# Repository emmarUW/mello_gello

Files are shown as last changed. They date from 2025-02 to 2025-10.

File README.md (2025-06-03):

# mello_gello
Improved models and methods for the Gello robot teleop system



# MELLO GELLO vs. GELLO

Inspired by and based on the original [GELLO project](https://wuphilipp.github.io/gello_site/).

## Key Improvements

- **Motors:** Uses [ROLLER485](https://shop.m5stack.com/products/rollercan-unit-with-bldc-motor-stm32) for better interface durability, I2C pass-through at similar price point
- **Linkages:** Swaps many fully 3D-printed parts with **Gobuilda 1121 aluminum rail** ([details](https://www.gobilda.com/1121-series-low-side-u-channel)).
- **Controller:** Upgraded from U2D2 to [M5 Stack Core3](https://docs.m5stack.com/en/core/CoreS3) with touchscreen, wireless OTA programming, and expanded connectivity.
- **Wireless:** Core3 onboard battery enables **15-20 min untethered runtime**, WiFi control, and flexible power options.
- **Tool Control:** Supports **any I2C input device**, expanding tool control capabilities.
- **Multi-Function Button:** Uses M5 **Key** to zero rotation or pause movement.

---

## Versions:

### UR5e:
The UR5 version of MG is *AVAILABLE* in the Universal Robots/UR5e folder - https://github.com/emmarUW/mello_gello/blob/main/Universal%20Robots/UR5e/README.md

### Franka:
The Franka version of MG is *IN WORK* - in the Franka folder

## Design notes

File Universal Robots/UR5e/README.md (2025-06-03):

UR5 BOM:

This UR5e is a 50%-scale teleop leader for the current model UR5e. All rotation centers should be spatially correct without any software compensation.



Fusion 360 Files - https://a360.co/4katDeD

Purchase:
- Gobuilda:
  - 1121-0008-216 X 1 - https://www.gobilda.com/1121-series-low-side-u-channel-8-hole-216mm-length/
  - 1121-0008-264 x 1 - https://www.gobilda.com/1121-series-low-side-u-channel-10-hole-264mm-length/

 - M5Stack via Digikey:
   - CoreS3 Controller x 1 - https://shop.m5stack.com/products/m5stack-cores3-esp32s3-lotdevelopment-kit
   - Roller485 x 6 - https://shop.m5stack.com/products/roller485-unit-with-bldc-motor-stm32
   - M5 Key x 1 - https://shop.m5stack.com/products/mechanical-key-button-unit
   - M5 Joystick2 x 1 - https://shop.m5stack.com/products/i2c-joystick-2-unit-stm32g030
  


Print:
  - Common Parts:
    - Base
    - Base Adapter
    - Handle Adapter
    - Handle

  - Links 1-5

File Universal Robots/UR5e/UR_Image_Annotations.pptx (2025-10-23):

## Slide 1

264mm/10 hole
Gobuilda
1121-0010-0264

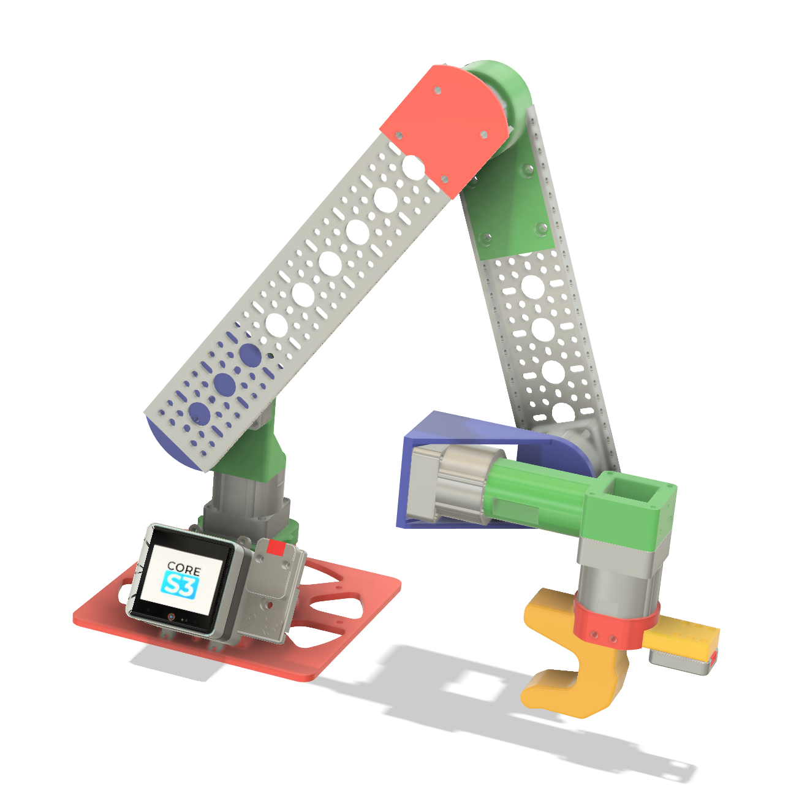
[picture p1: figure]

216mm/8 hole
Gobuilda
1121-0008-0216

DIN RAIL

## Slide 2

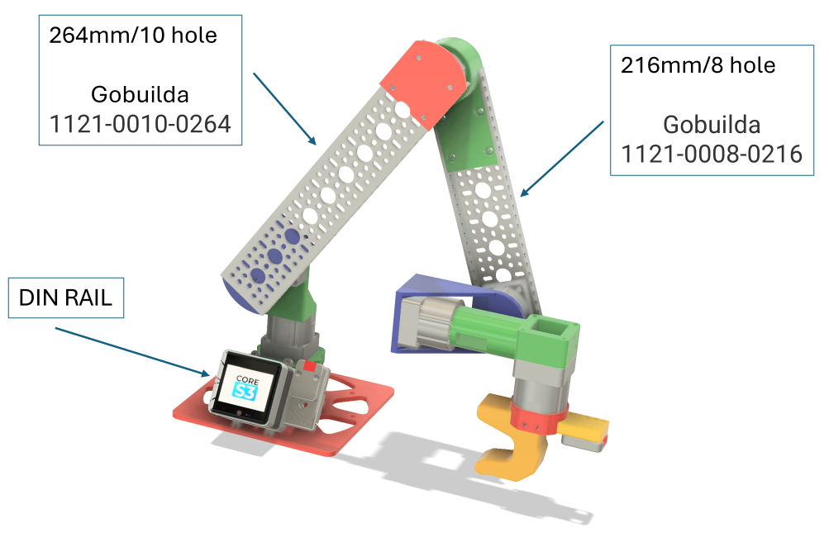
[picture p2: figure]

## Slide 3

264mm/10 hole
Gobuilda
1121-0010-0264

Link_3.stl

216mm/8 hole
Gobuilda
1121-0008-0216

Link_3.stl

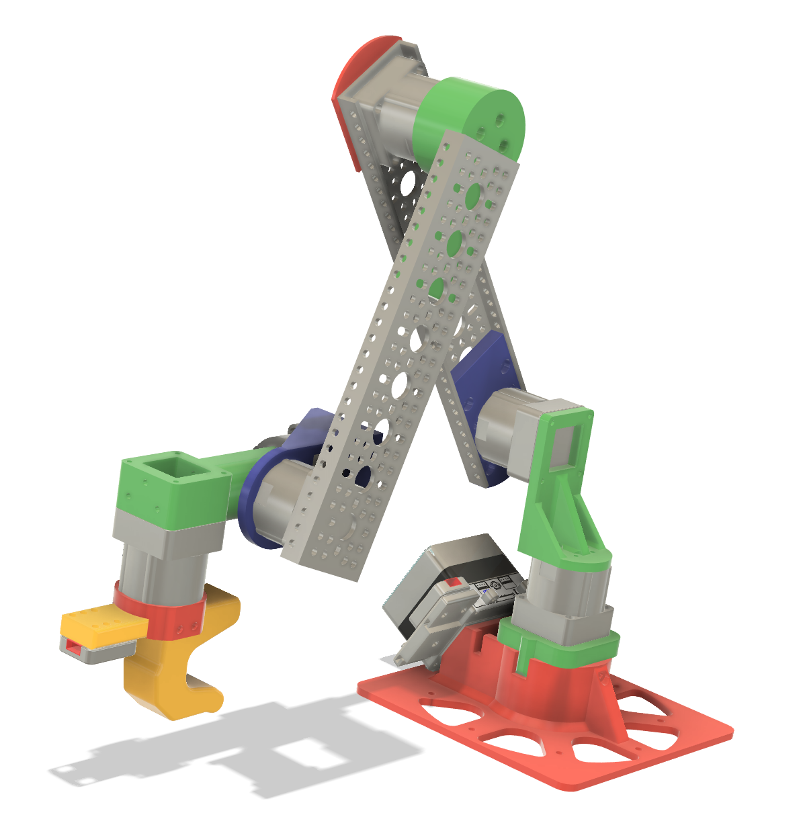
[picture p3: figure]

Common Parts/M5_compatible_handle/*

Link_4.stl

Link_2.stl

Link_7.stl

Link_1.stl

/Common Parts/Base/*

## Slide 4

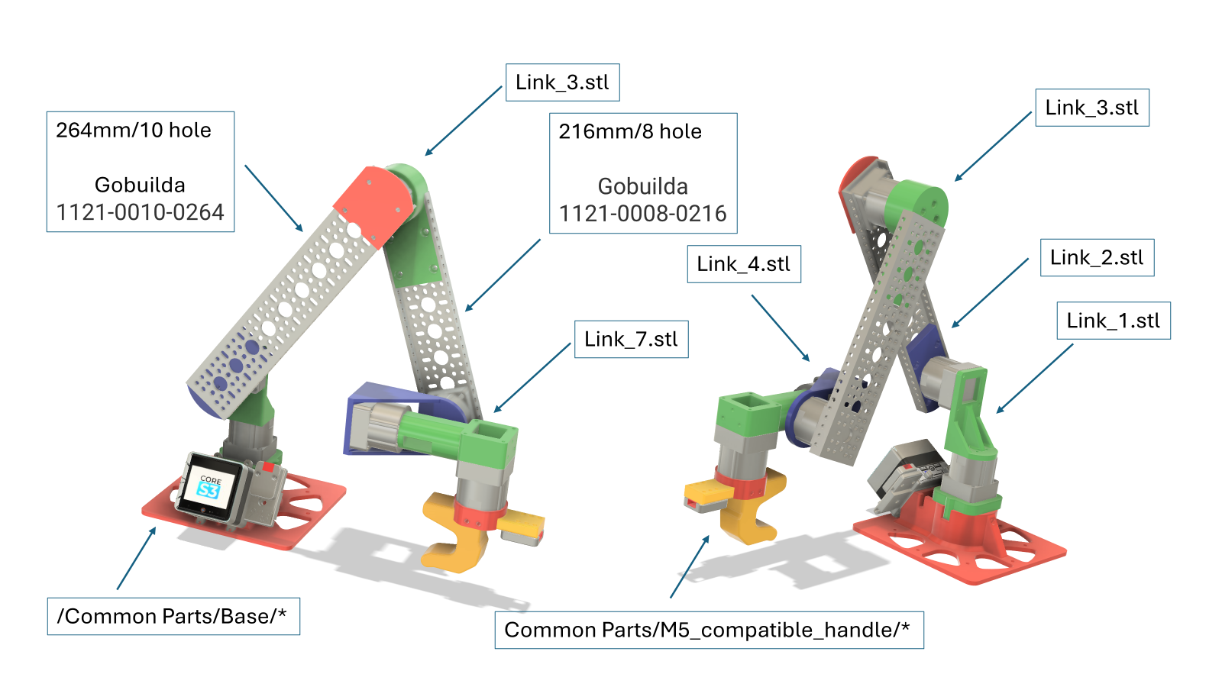
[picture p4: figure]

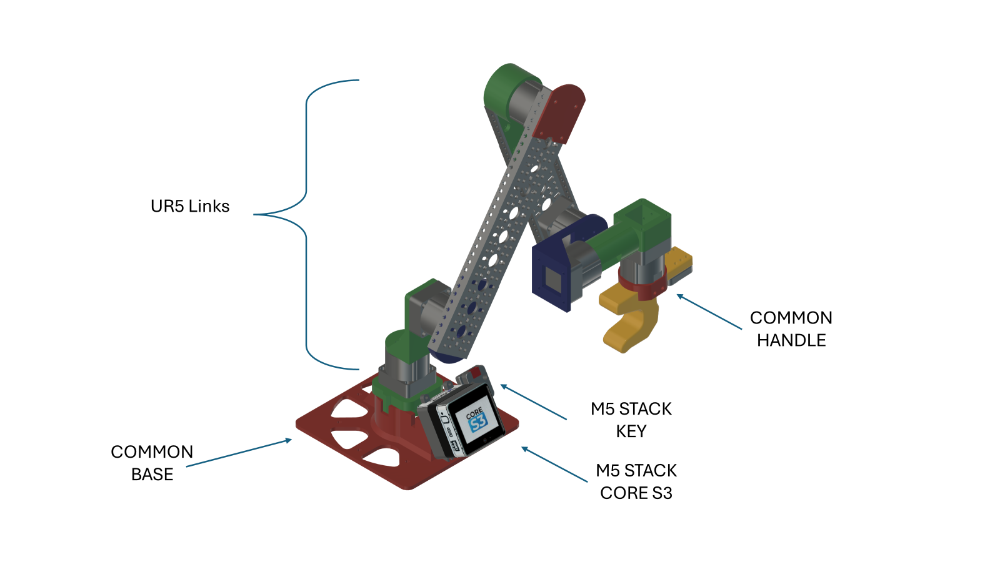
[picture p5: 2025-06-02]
Readme_Schematic.png

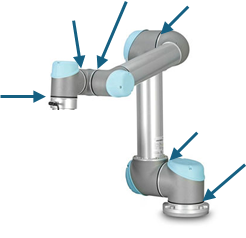
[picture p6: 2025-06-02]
Universal Robots/UR5e/UR.png

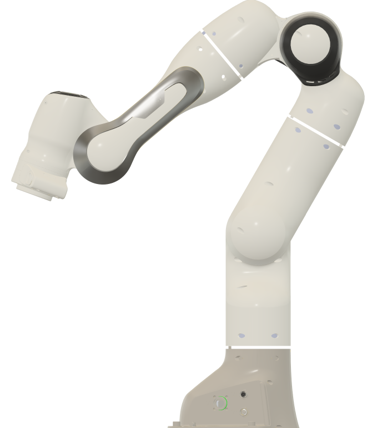
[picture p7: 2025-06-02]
Franka/CAD_franka.png

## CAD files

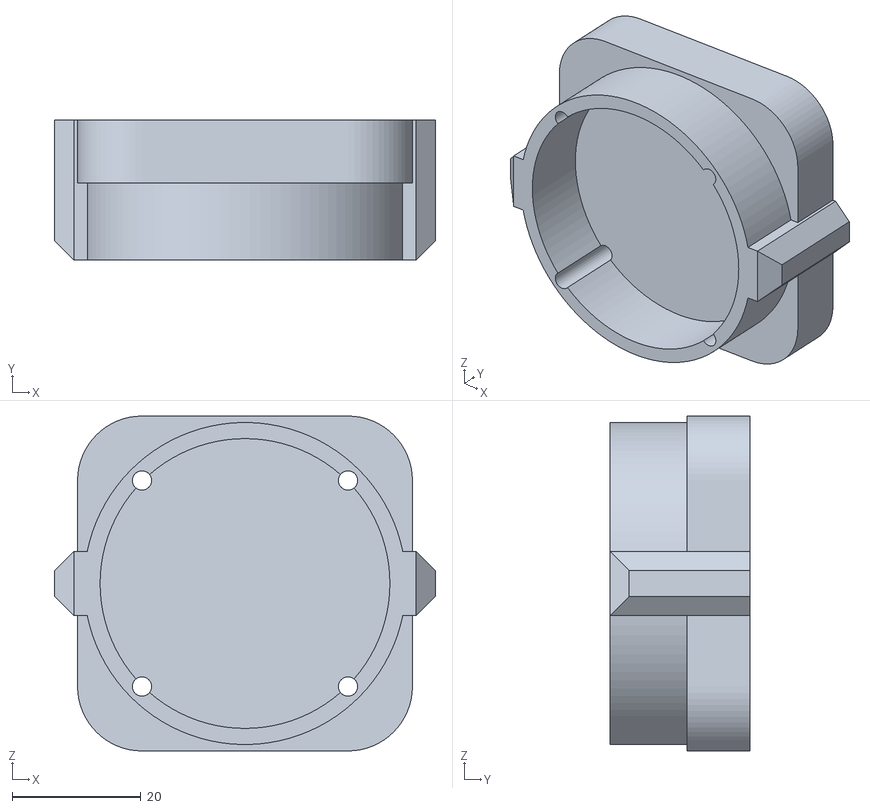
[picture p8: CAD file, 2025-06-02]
Common Parts/Base/base_adapter.stl
59.2 x 21.8 x 52.0

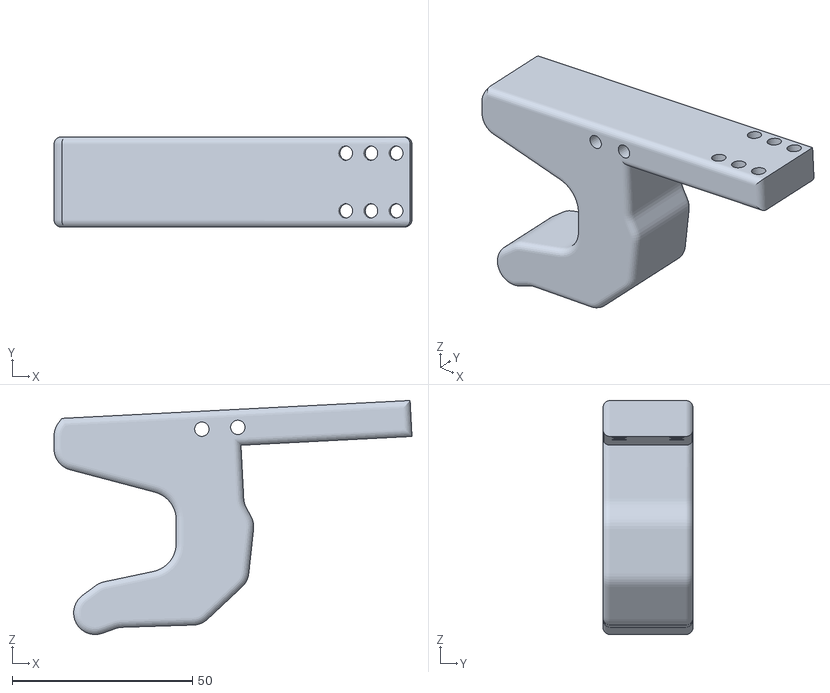
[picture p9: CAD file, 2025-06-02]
Common Parts/M5_compatible_handle/handle_body.stl
99.3 x 25.0 x 64.9

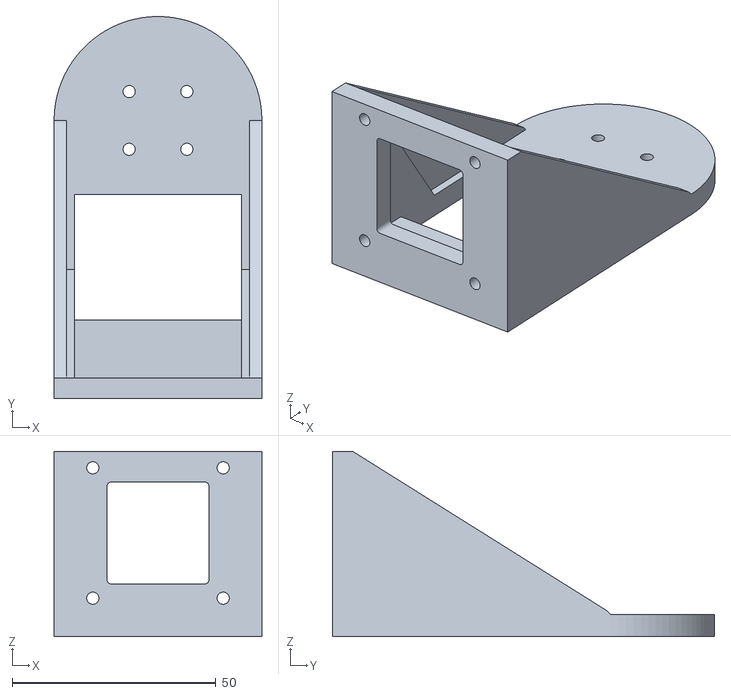
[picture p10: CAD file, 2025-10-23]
Universal Robots/UR5e/Link_4.stl
51.0 x 93.7 x 45.4

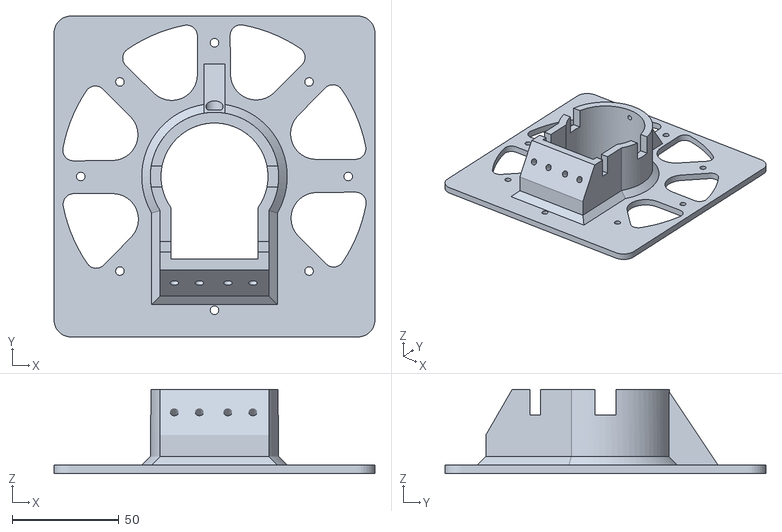
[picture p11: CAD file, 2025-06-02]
Common Parts/Base/Clamp_down_base.stl
150.0 x 150.0 x 39.3

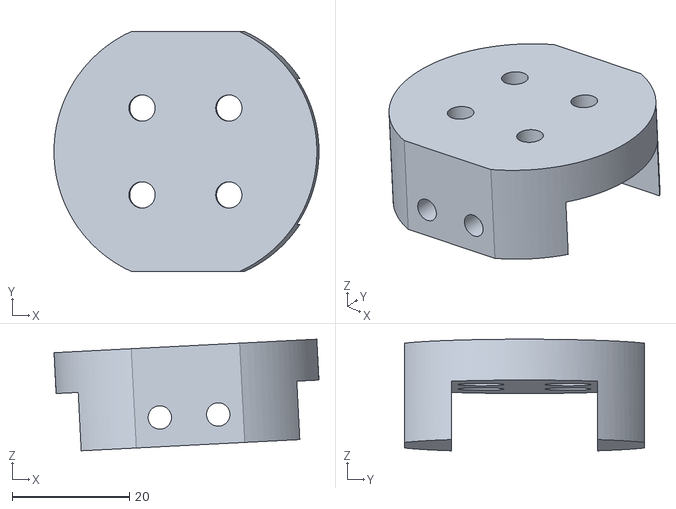
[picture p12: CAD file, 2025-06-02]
Common Parts/M5_compatible_handle/handle_to_motor_adapter.stl
45.3 x 41.0 x 19.1

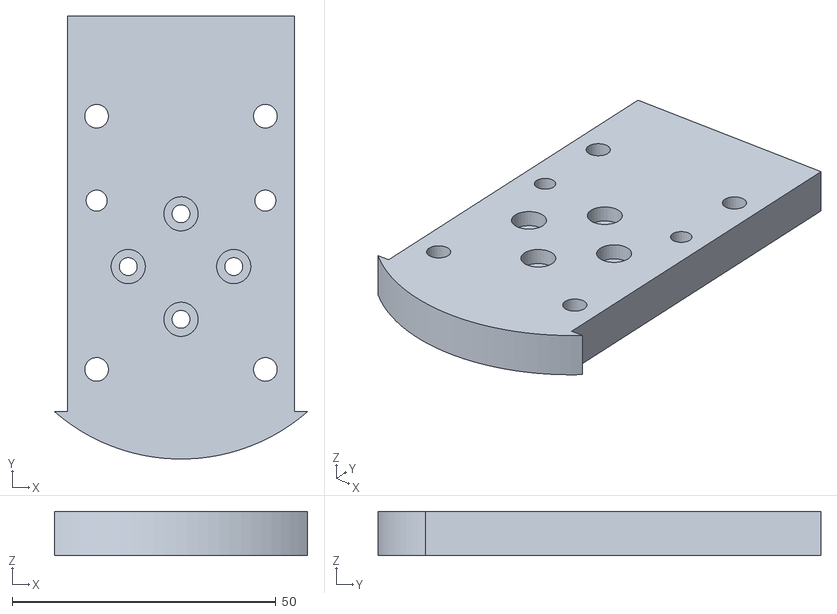
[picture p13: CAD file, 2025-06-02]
Universal Robots/UR5e/Link_2.stl
48.0 x 84.0 x 8.40

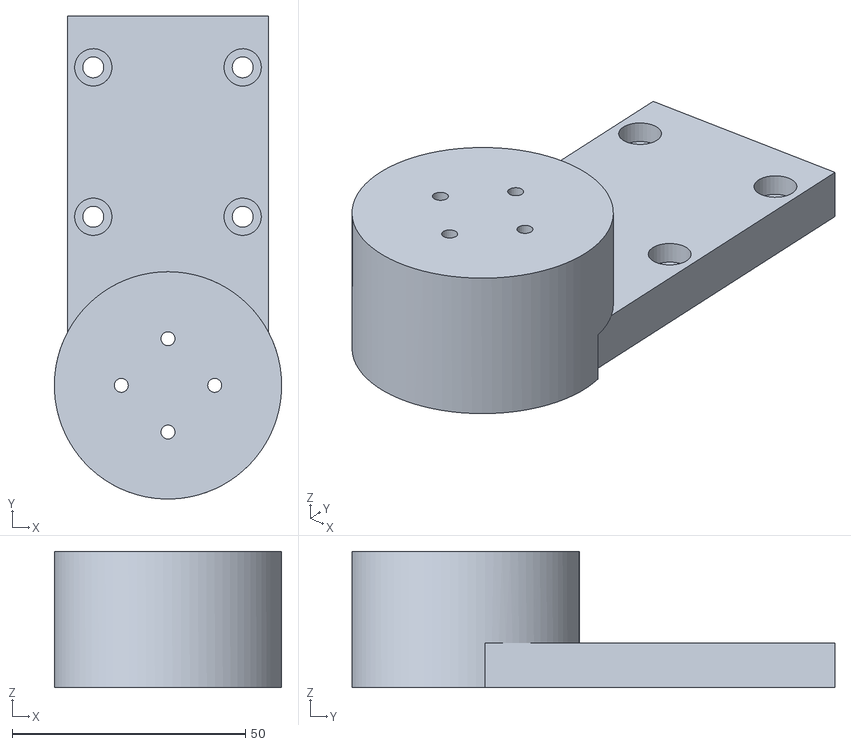
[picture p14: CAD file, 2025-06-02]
Universal Robots/UR5e/Link_3.stl
48.7 x 103.5 x 29.1

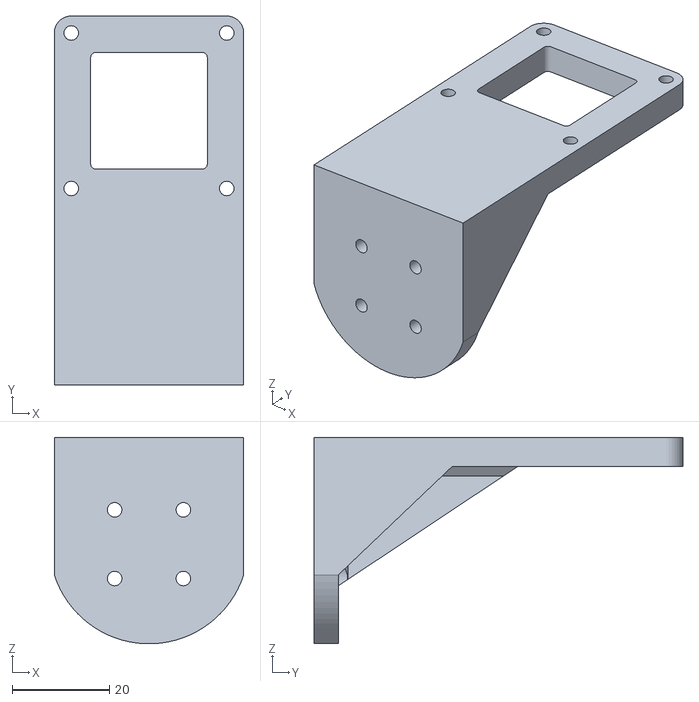
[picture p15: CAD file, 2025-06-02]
Universal Robots/UR5e/Link_1.stl
39.0 x 76.0 x 42.5

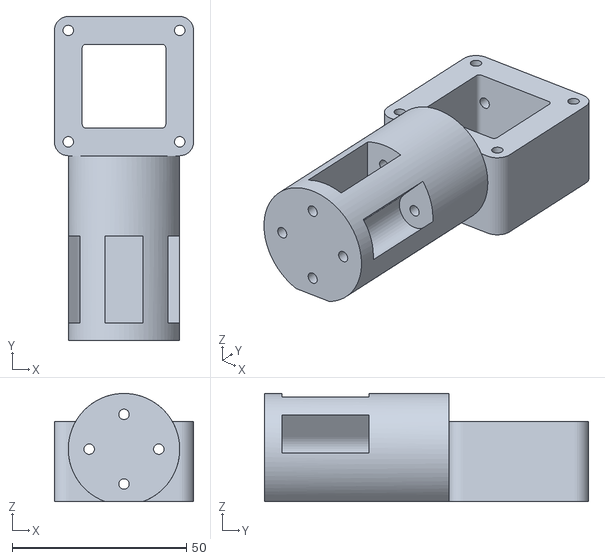
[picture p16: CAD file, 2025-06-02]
Universal Robots/UR5e/Link_7.stl
40.0 x 93.1 x 31.0

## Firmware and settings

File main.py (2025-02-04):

import os, sys, io
import M5
from M5 import *
from unit import KeyUnit
import time
import network
from unit import RollerCANUnit
from hardware import I2C
from hardware import Pin



label_pwr_status = None
label0 = None
label1 = None
label3 = None
title_bar = None
label_zerod = None
label2 = None
label4 = None
image0 = None
label_position_linked = None
label6 = None
label_wifi_status = None
label5 = None
label_stream_state = None
wlan = None
i2c0 = None
key_0 = None
rollercan_0 = None
rollercan_1 = None
rollercan_2 = None
rollercan_3 = None


stream_is_paused = None
k = None
joint_init_pos = None
joint_reported_position = None
joint_values_measured = None
joint_signs = None

# Describe this function...
def calc_position():
  global stream_is_paused, k, joint_init_pos, joint_reported_position, joint_values_measured, joint_signs, label_pwr_status, label0, label1, label3, title_bar, label_zerod, label2, label4, image0, label_position_linked, label6, label_wifi_status, label5, label_stream_state, wlan, i2c0, key_0, rollercan_0, rollercan_1, rollercan_2, rollercan_3
  for k in range(7):
    joint_reported_position[int(k - 1)] = joint_init_pos[int(k - 1)] + joint_signs[int(k - 1)] * joint_values_measured[int(k - 1)]


# Describe this function...
def init_position():
  global stream_is_paused, k, joint_init_pos, joint_reported_position, joint_values_measured, joint_signs, label_pwr_status, label0, label1, label3, title_bar, label_zerod, label2, label4, image0, label_position_linked, label6, label_wifi_status, label5, label_stream_state, wlan, i2c0, key_0, rollercan_0, rollercan_1, rollercan_2, rollercan_3
  joint_init_pos = [rollercan_0.get_motor_position_readback(), rollercan_1.get_motor_position_readback(), rollercan_2.get_motor_position_readback(), rollercan_3.get_motor_position_readback(), 0, 0, 0]
  time.sleep_ms(100)


def key_0_wasPressed_event(state):
  global label_pwr_status, label0, label1, label3, title_bar, label_zerod, label2, label4, image0, label_position_linked, label6, label_wifi_status, label5, label_stream_state, wlan, i2c0, key_0, rollercan_0, rollercan_1, rollercan_2, rollercan_3, stream_is_paused, joint_init_pos, joint_reported_position, k, joint_values_measured, joint_signs
  key_0.set_color(0x33ff33)
  label_zerod.setColor(0xffffff, 0x33cc00)
  init_position()


def key_0_wasDoubleclicked_event(state):
  global label_pwr_status, label0, label1, label3, title_bar, label_zerod, label2, label4, image0, label_position_linked, label6, label_wifi_status, label5, label_stream_state, wlan, i2c0, key_0, rollercan_0, rollercan_1, rollercan_2, rollercan_3, stream_is_paused, joint_init_pos, joint_reported_position, k, joint_values_measured, joint_signs
  stream_is_paused = not stream_is_paused
  if stream_is_paused:
    key_0.set_color(0xffcc00)
    label_stream_state.setColor(0xffffff, 0xffcc00)
  else:
    key_0.set_color(0x33ff33)
    label_stream_state.setColor(0xffffff, 0x33cc00)


def setup():
  global label_pwr_status, label0, label1, label3, title_bar, label_zerod, label2, label4, image0, label_position_linked, label6, label_wifi_status, label5, label_stream_state, wlan, i2c0, key_0, rollercan_0, rollercan_1, rollercan_2, rollercan_3, stream_is_paused, joint_init_pos, joint_reported_position, k, joint_values_measured, joint_signs

  M5.begin()
  Widgets.fillScreen(0xffffff)
  label_pwr_status = Widgets.Label("pwr", 1, 41, 1.0, 0x008616, 0xffffff, Widgets.FONTS.DejaVu12)
  label0 = Widgets.Label("0", 262, 192, 1.0, 0x008616, 0xffffff, Widgets.FONTS.DejaVu18)
  label1 = Widgets.Label("1", 254, 141, 1.0, 0x008616, 0xffffff, Widgets.FONTS.DejaVu18)
  label3 = Widgets.Label("3", 269, 37, 1.0, 0x008616, 0xffffff, Widgets.FONTS.DejaVu18)
  title_bar = Widgets.Title("MELLO GELLO - FRANKA", 3, 0xffffff, 0x8e8e92, Widgets.FONTS.DejaVu18)
  label_zerod = Widgets.Label("ZERO'D", 7, 216, 1.0, 0xffffff, 0xff0000, Widgets.FONTS.DejaVu12)
  label2 = Widgets.Label("2", 271, 79, 1.0, 0x008616, 0xffffff, Widgets.FONTS.DejaVu18)
  label4 = Widgets.Label("4", 227, 50, 1.0, 0x008616, 0xffffff, Widgets.FONTS.DejaVu18)
  image0 = Widgets.Image("res/img/CAD_franka.png", 139, 23, scale_x=.5, scale_y=.5)
  label_position_linked = Widgets.Label("POSITION LINKED", 83, 217, 1.0, 0xffffff, 0xff0000, Widgets.FONTS.DejaVu12)
  label6 = Widgets.Label("6", 155, 102, 1.0, 0x008616, 0xffffff, Widgets.FONTS.DejaVu18)
  label_wifi_status = Widgets.Label("Wifi_status", 2, 25, 1.0, 0x008616, 0xffffff, Widgets.FONTS.DejaVu12)
  label5 = Widgets.Label("5", 197, 85, 1.0, 0x008616, 0xffffff, Widgets.FONTS.DejaVu18)
  label_stream_state = Widgets.Label("STREAMING", 223, 217, 1.0, 0xffffff, 0xff0000, Widgets.FONTS.DejaVu12)

  wlan = network.WLAN(network.STA_IF)
  i2c0 = I2C(0, scl=Pin(1), sda=Pin(2), freq=100000)
  key_0 = KeyUnit((8, 9))
  key_0.setCallback(type=key_0.CB_TYPE.WAS_PRESSED, cb=key_0_wasPressed_event)
  key_0.setCallback(type=key_0.CB_TYPE.WAS_DOUBLECLICKED, cb=key_0_wasDoubleclicked_event)
  rollercan_2 = RollerCANUnit(i2c0, address=0x66, mode=RollerCANUnit.I2C_MODE)
  rollercan_1 = RollerCANUnit(i2c0, address=0x65, mode=RollerCANUnit.I2C_MODE)
  rollercan_0 = RollerCANUnit(i2c0, address=0x64, mode=RollerCANUnit.I2C_MODE)
  rollercan_3 = RollerCANUnit(i2c0, address=0x67, mode=RollerCANUnit.I2C_MODE)
  joint_values_measured = [0] * 7
  joint_init_pos = [0] * 7
  joint_reported_position = [0] * 7
  joint_signs = [-1, -1, -1, -1, 1, 1, 1]
  try:
    wlan.connect('SSID', 'PWD')
    label_wifi_status.setText(str((str('IP: ') + str((wlan.ifconfig()[0])))))
  except:
    pass

  rollercan_0.set_motor_output_state(1)
  rollercan_1.set_motor_output_state(1)
  rollercan_2.set_motor_output_state(1)
  rollercan_3.set_motor_output_state(1)
  rollercan_2.set_motor_mode(4)
  rollercan_0.set_motor_mode(4)
  rollercan_1.set_motor_mode(4)
  rollercan_2.set_motor_mode(4)
  rollercan_3.set_motor_mode(4)
  key_0.set_color(0xff6600)
  stream_is_paused = True
  init_position()


def loop():
  global label_pwr_status, label0, label1, label3, title_bar, label_zerod, label2, label4, image0, label_position_linked, label6, label_wifi_status, label5, label_stream_state, wlan, i2c0, key_0, rollercan_0, rollercan_1, rollercan_2, rollercan_3, stream_is_paused, joint_init_pos, joint_reported_position, k, joint_values_measured, joint_signs
  key_0.tick(None)
  M5.update()
  joint_values_measured = [rollercan_0.get_motor_position_readback(), rollercan_1.get_motor_position_readback(), rollercan_2.get_motor_position_readback(), rollercan_3.get_motor_position_readback(), 0, 0, 0]
  if not stream_is_paused:
    calc_position()
    print({'iniital_positions':joint_init_pos,'measured_positions':joint_values_measured,'joint_positions:':joint_reported_position})
    time.sleep_ms(100)
  label0.setText(str(joint_reported_position[0]))
  label1.setText(str(joint_reported_position[1]))
  label2.setText(str(joint_reported_position[2]))
  label3.setText(str(joint_reported_position[3]))
  label4.setText(str('NA'))
  label5.setText(str('NA'))
  label6.setText(str('NA'))
  label_pwr_status.setText(str((str('BAT % : ') + str((Power.getBatteryLevel())))))


if __name__ == '__main__':
  try:
    setup()
    while True:
      loop()
  except (Exception, KeyboardInterrupt) as e:
    try:
      from utility import print_error_msg
      print_error_msg(e)
    except ImportError:
      print("please update to latest firmware")

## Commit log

2025-06-02 Commit of UR and common geometry
    Adding all UR5 and common STL files
    [Clamp_down_base.stl, Link_1.stl, Link_2.stl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]
2025-06-02 Update README.md
    Added schematic drawing
2025-06-02 Renumber UR Links
    [Link_3.stl, Link_4.stl, Link_5.stl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]
2025-06-09 file fix
    [Link_7.stl]
2025-10-23 Update Link_4.stl
    Added additional gussets to increase part strength
    [Link_4.stl]
2025-10-23 Added assembly images
    images of assembled UR5 MG with 3D printed and metal parts annotated
2025-10-23 Create UR_Image_Annotations.pptx
    Editable PPT with images of UR assembly
